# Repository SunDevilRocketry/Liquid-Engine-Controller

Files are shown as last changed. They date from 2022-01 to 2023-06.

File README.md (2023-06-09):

<h1>Liquids Engine Controller</h1>

<p>Current PCB Revision: 5.1</p>
<p>PCB Part Number: L0002</p>

<p>The Liquid Engine Controller is the main embedded processor of Sun Devil Rocketry's Liquid Engine. As the brains of the engine, the controller is responsible for executing propellant feed sequences semi-autonomously, logging sensor data, and transmitting engine telemetry. The controller is equipped with an STM32 ARM Cortex M7 processor and 4Mb of external flash for data logging. The board includes a micro-SD card jack for easy access to the logged data. The board includes many power sources for flexible use of the controller during testing and normal operation. These include a 12V power jack, a USB Type B connector, and a 2-pin male pin header. The board includes short circuit protection on the main power rail and regulates the multiplexed supply to 5V and 3.3V with a buck converter and linear regulator (LDO) respectively. The board interfaces with a PC through either the USB port or the 8-pin telemetry connector, which allows wireless transceiver modules with either a UART or SPI interface to be connected. The screw terminals on the board connect to the ignition circuitry. An e-match is used to initiate combustion, and two continuity wires are used to provide the controller feedback on the ignition state. The ignition current is routed through an additional screw terminal which serves as a safety/arming switch. The board interfaces with all of the engine sensors, including eight pressure transducers, a thermocouple, and a load cell. The pressure transducer outputs are amplified with a programmable-gain instrumentation amplifier, which allows for up to 256 calibration settings. The thermocouple output is processed using a cold-junction compensation IC. Additionally, the board includes a reset button and several LEDs for visual indication of power and firmware status.
</p>

<p><b>Working Directory Structure:</b></p>

<p>
   cad: 3d models

   doc: documentation

   img: images of circuit/footprints for github display 
   
   lib: libraries for schematic symbols and footprints

   production: files needed for pcb fabrication, e.g. gerbers, profile, drill file

   sim: simulation models/files 

   src: source design files, e.g. schematic and PCB layout files
</p>

<h2>3D Model: </h2>

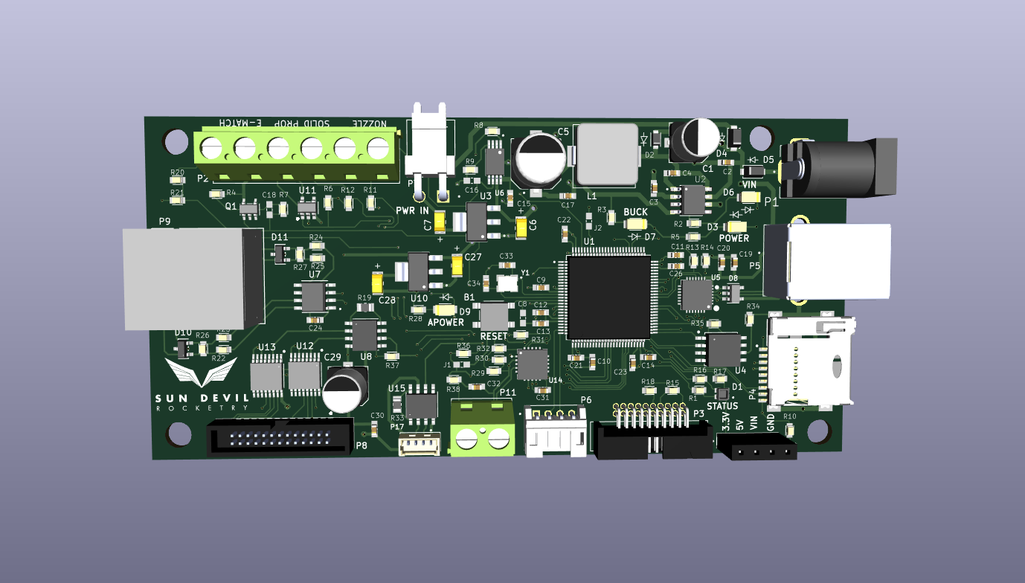
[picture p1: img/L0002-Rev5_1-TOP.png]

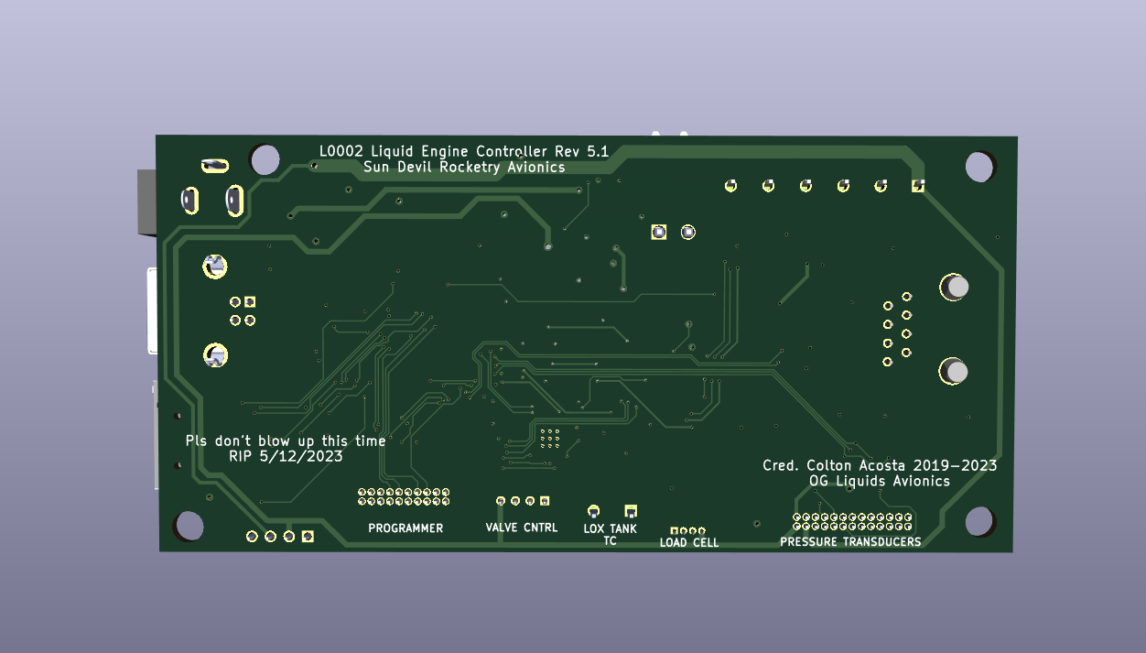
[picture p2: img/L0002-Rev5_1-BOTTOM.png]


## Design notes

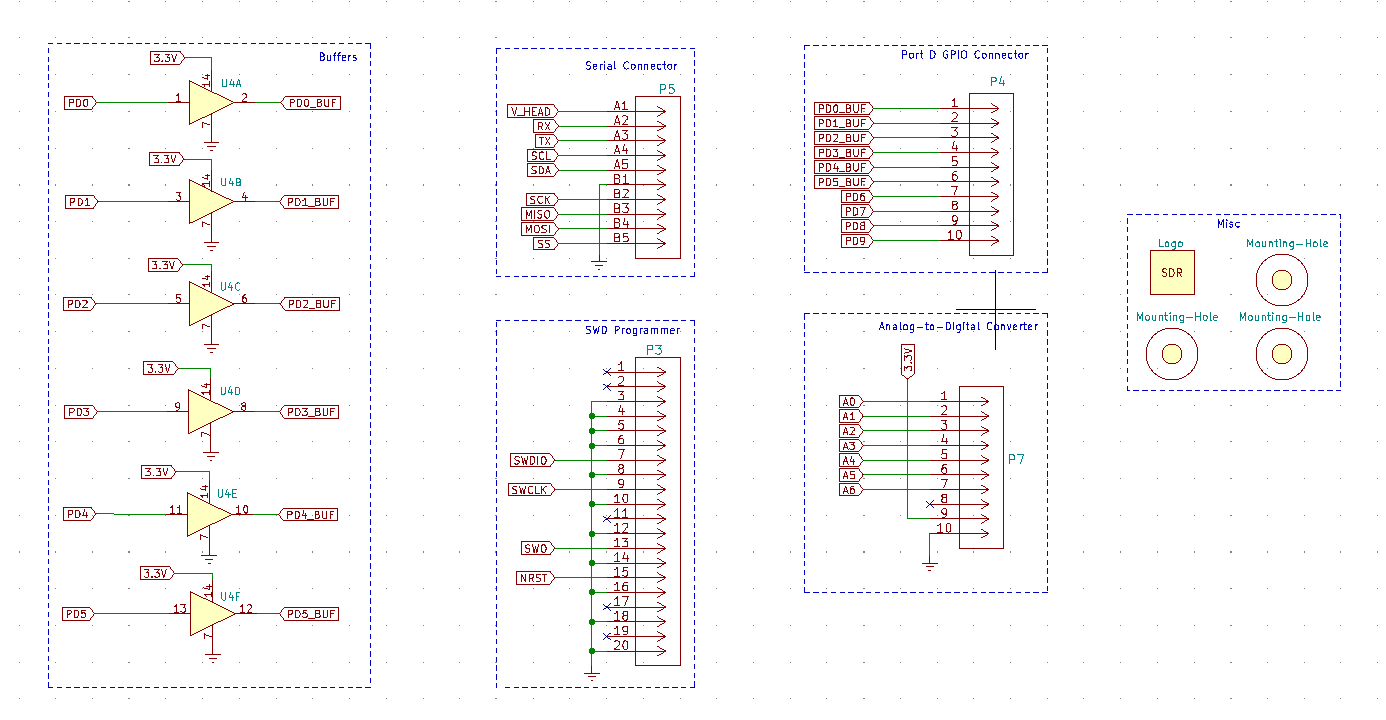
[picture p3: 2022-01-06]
img/Connectors-Schematic.png

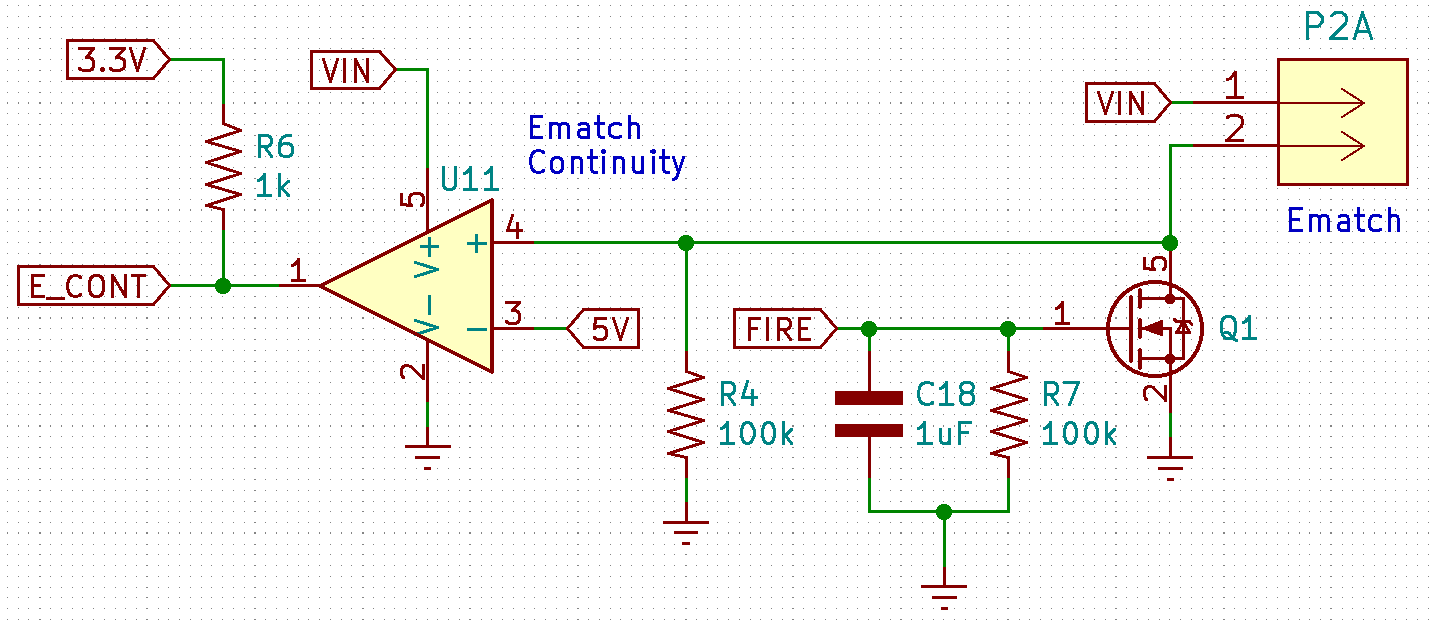
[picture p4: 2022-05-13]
img/Ignition-Schematic.png

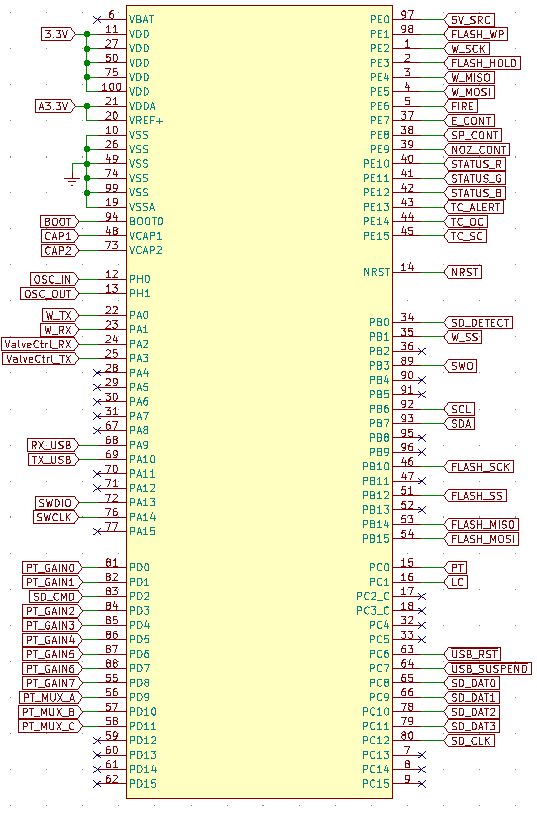
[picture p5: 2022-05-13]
img/MCU-Schematic.png

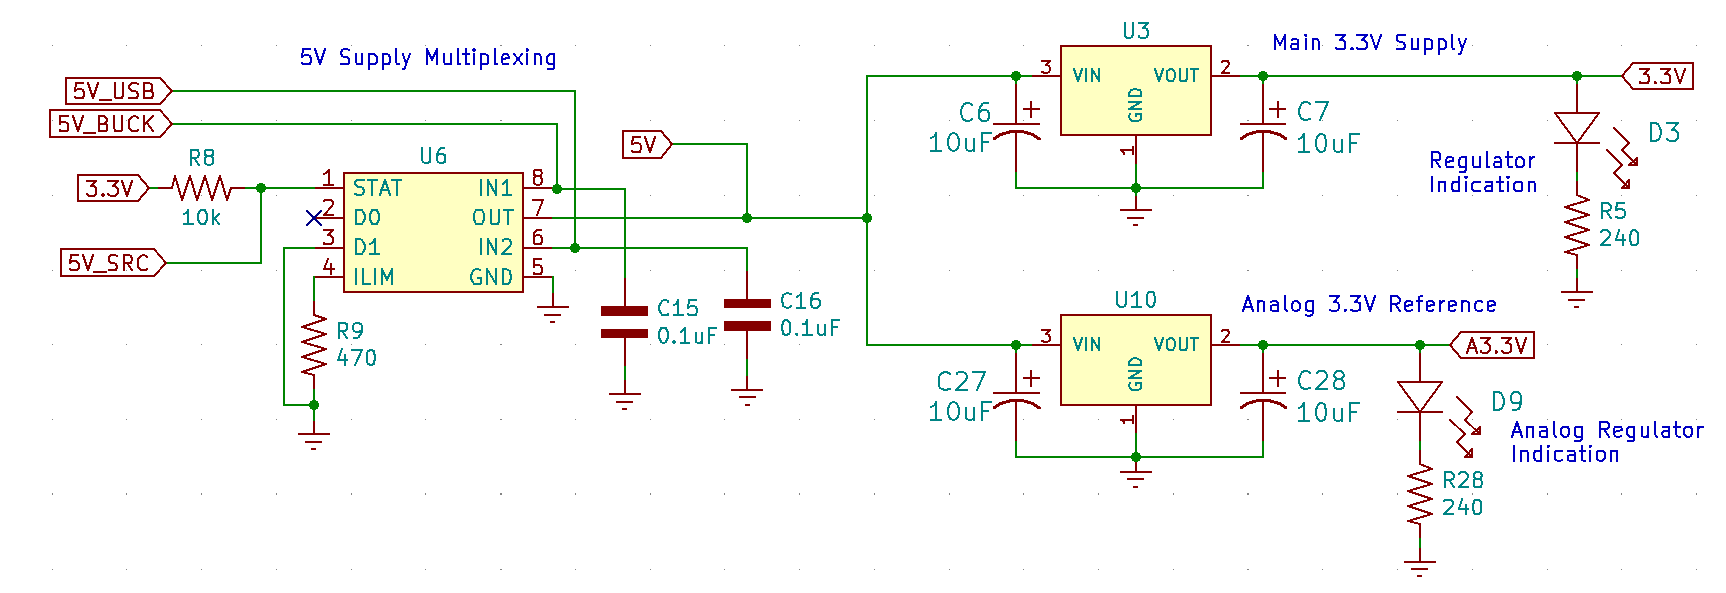
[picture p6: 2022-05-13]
img/3V3-Schematic.png

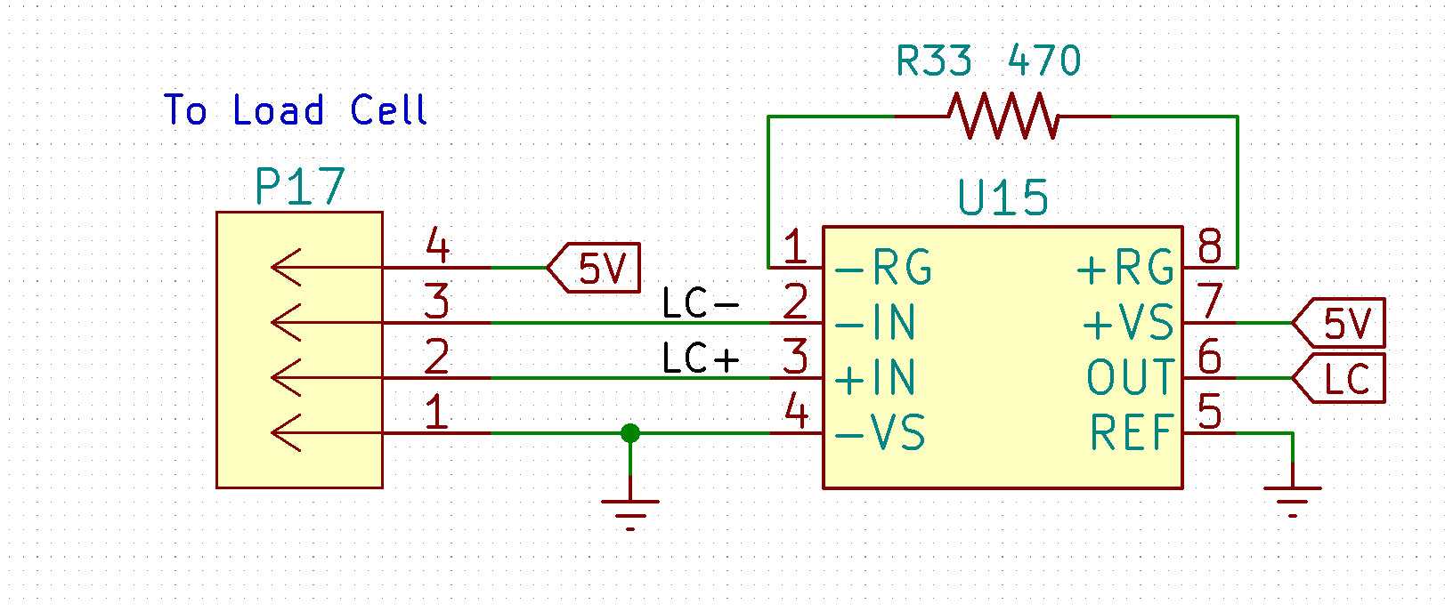
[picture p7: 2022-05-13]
img/Load-Cell-Schematic.png

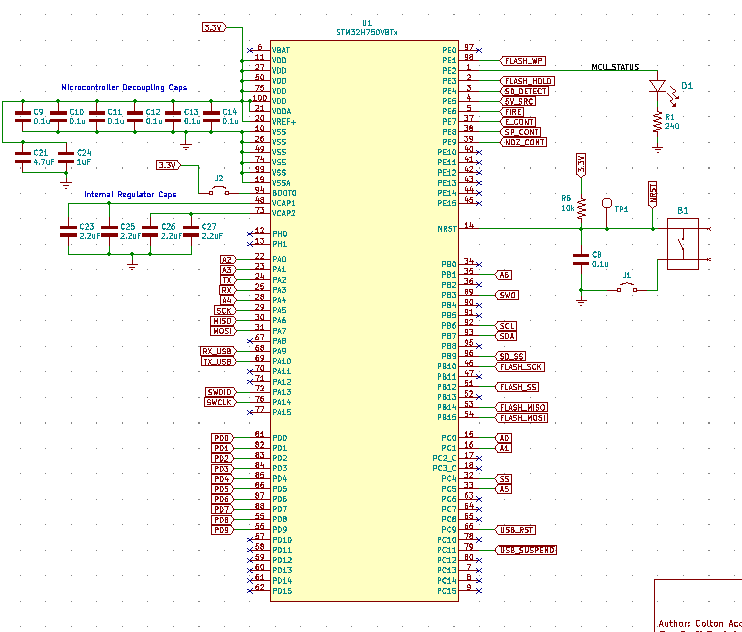
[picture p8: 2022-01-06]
img/Micro-Schematic.png

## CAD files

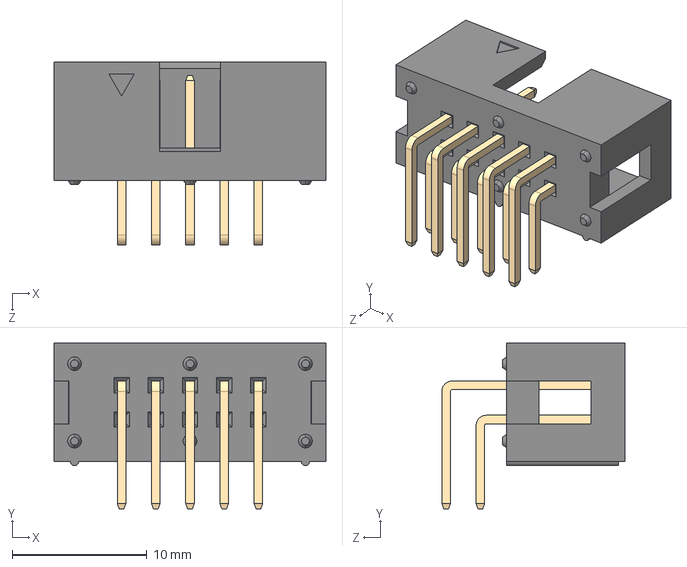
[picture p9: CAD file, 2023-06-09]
CAD/3Dfiles/SBH11-PBPC-D05-RA-BK.STEP
20.2 x 12.3 x 13.6 mm

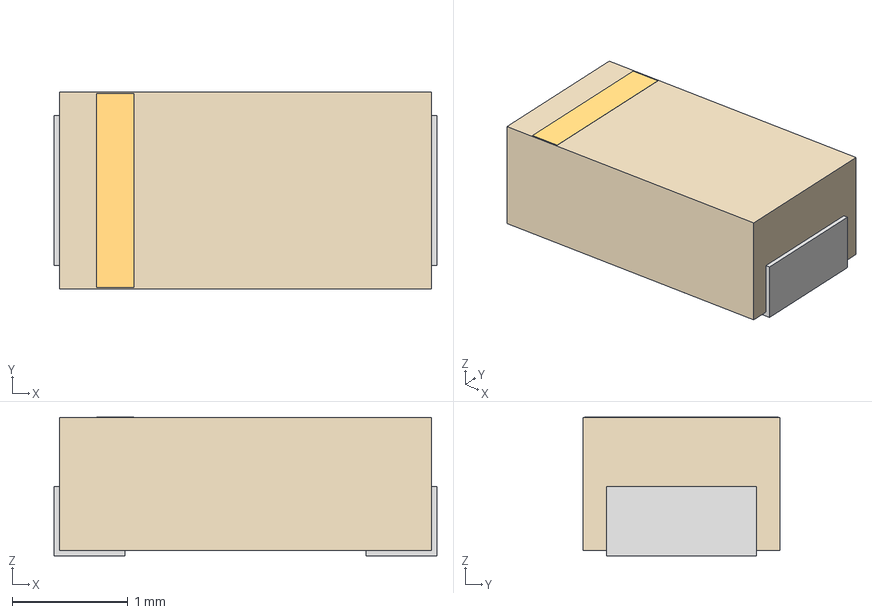
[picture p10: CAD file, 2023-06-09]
CAD/3Dfiles/LED_LTST-C150GKT_LTO.step
3.30 x 1.70 x 1.20 mm

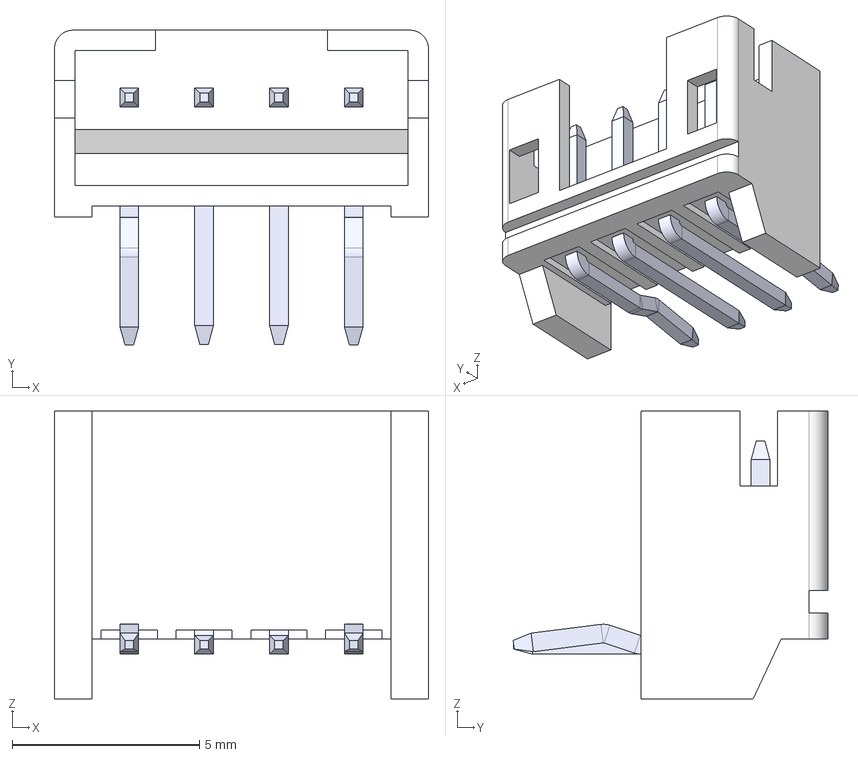
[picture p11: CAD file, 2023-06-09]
CAD/3Dfiles/140-504-415-000.step
10.0 x 8.41 x 7.70 mm
RA Housing_504
RA Contact_Kink
RA Contact_Str
RA Contact_Str001
RA Contact_Kink001

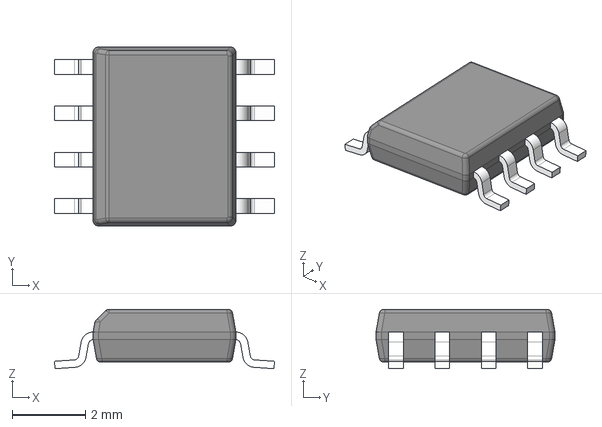
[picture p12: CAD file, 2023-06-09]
CAD/3Dfiles/sn65hcd71.step
6.02 x 4.90 x 1.63 mm
BODY-SO
LEAD-D0008A x 8

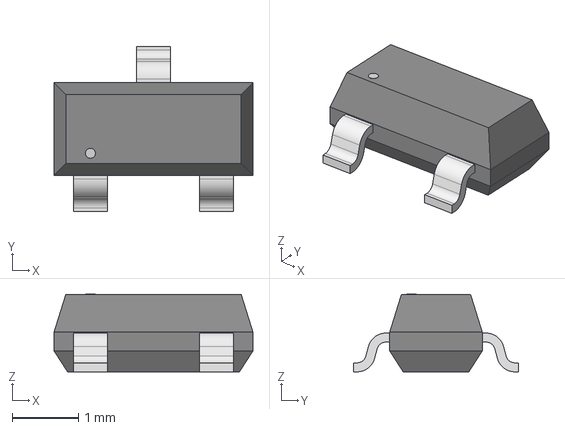
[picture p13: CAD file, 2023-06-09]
CAD/3Dfiles/CDSOT23-SM712.step
3.00 x 2.49 x 1.17 mm

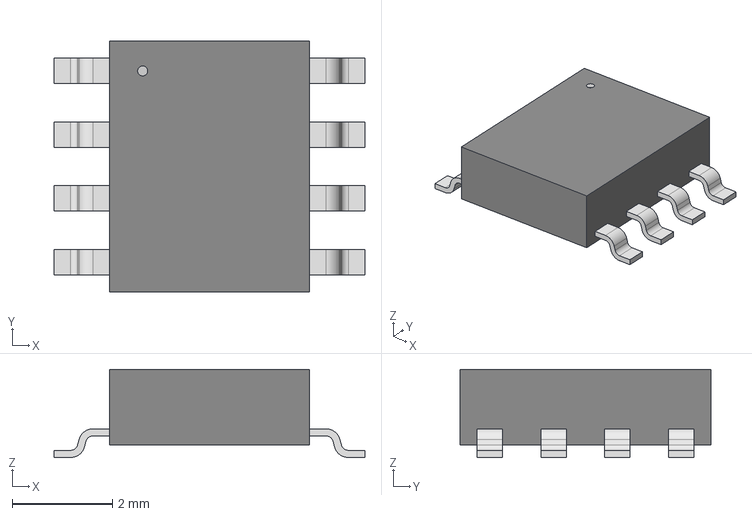
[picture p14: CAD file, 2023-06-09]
CAD/3Dfiles/AD623ARZ-R7.step
6.20 x 5.00 x 1.75 mm

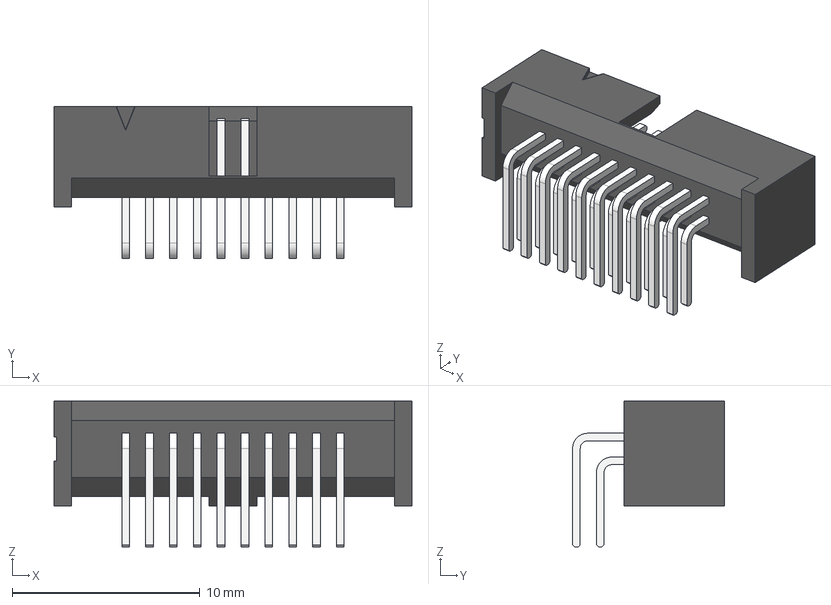
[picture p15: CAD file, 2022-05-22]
CAD/3Dfiles/3220-20-0200-00.stp
19.1 x 8.08 x 7.75 mm
_SHF-110-01-D_header
_SHF-First_Position_Indicator
_T-1S71-02-10-D-RA

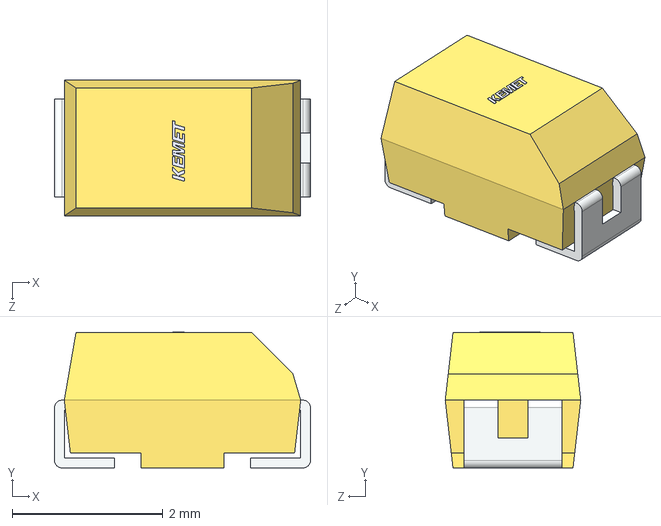
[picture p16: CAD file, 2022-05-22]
CAD/3Dfiles/T491A106K010AT.step
3.40 x 1.81 x 1.80 mm

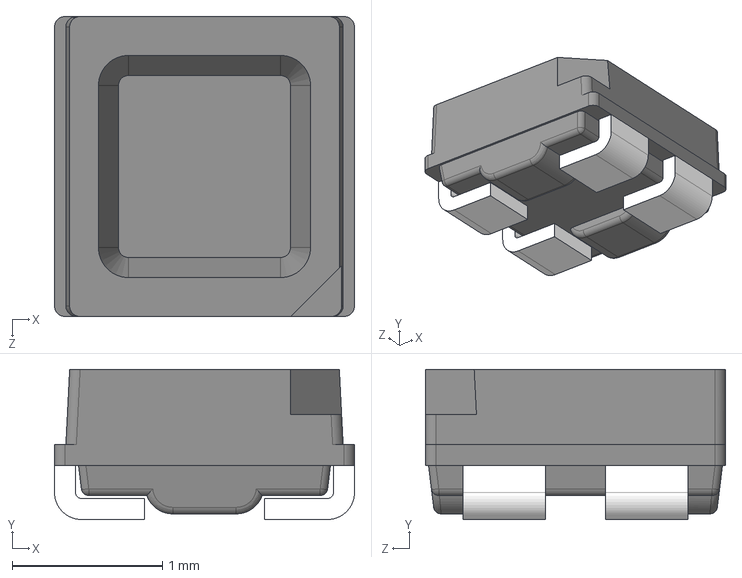
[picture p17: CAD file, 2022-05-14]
CAD/3Dfiles/CLMVC-FKA-CL1D1L71BB7C3C3.STEP
2.00 x 1 x 2.00 mm

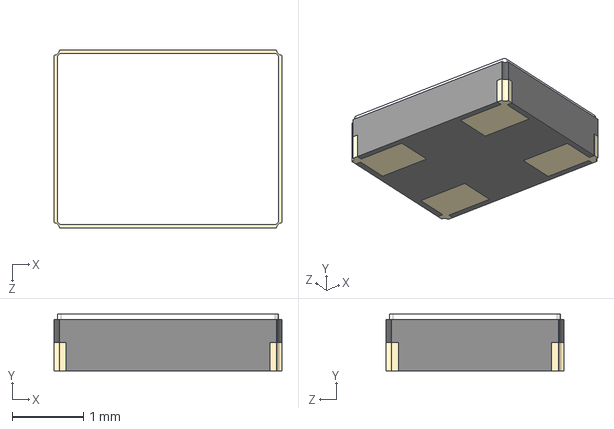
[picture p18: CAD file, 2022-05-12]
CAD/3Dfiles/ECS-240-18-33-JGN-TR.STEP
3.20 x 0.8 x 2.50 mm

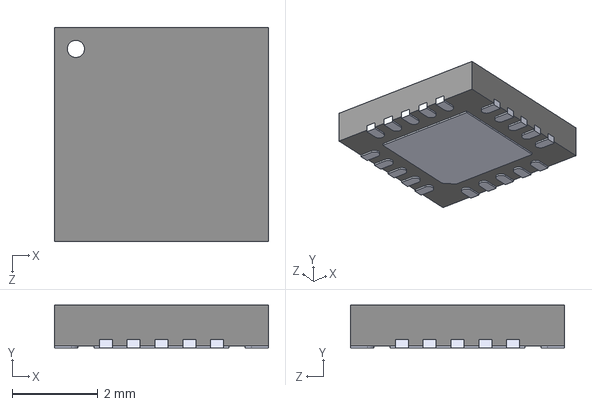
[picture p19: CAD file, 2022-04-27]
CAD/3Dfiles/MCP96L01T-E_MX.step
5.00 x 1.00 x 5.00 mm

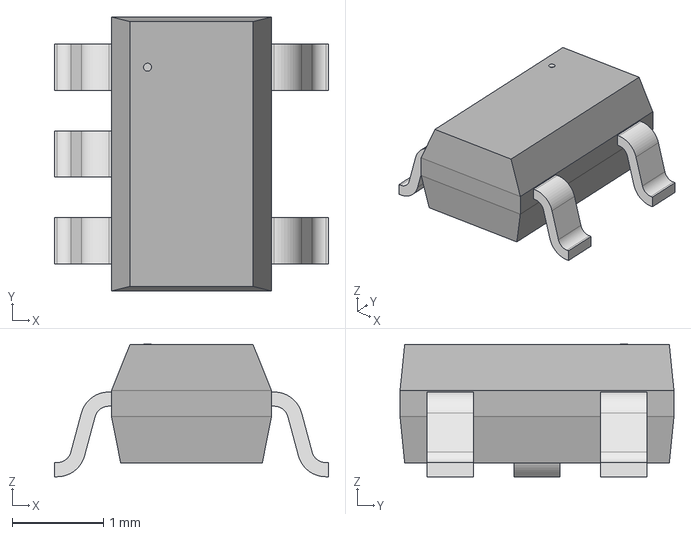
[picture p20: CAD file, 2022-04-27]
CAD/3Dfiles/TS391lYLT.step
3.00 x 3.00 x 1.45 mm

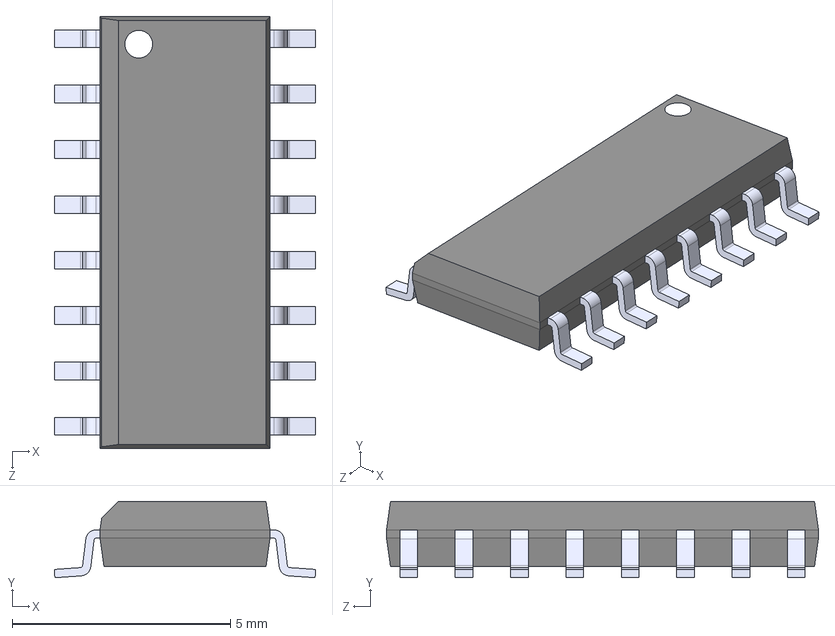
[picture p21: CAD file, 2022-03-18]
CAD/3Dfiles/CD74HC238M.STEP
5.99 x 1.75 x 9.91 mm

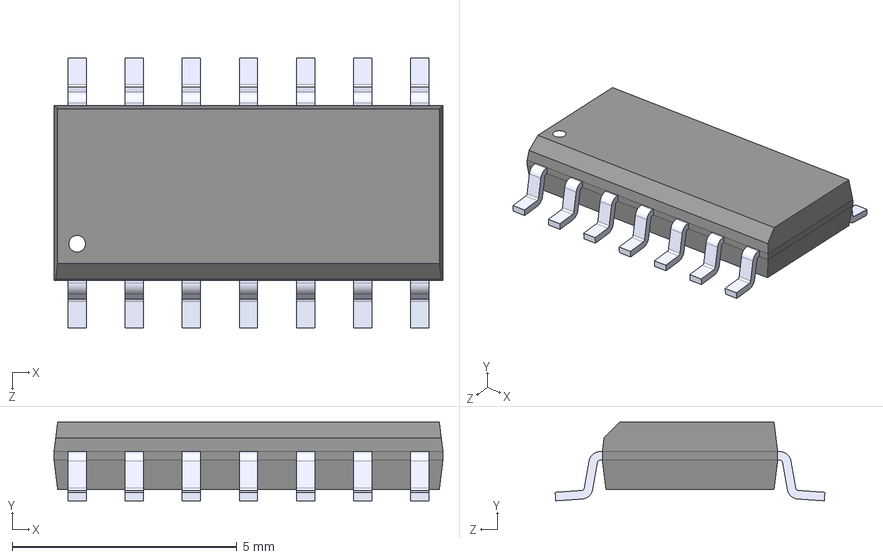
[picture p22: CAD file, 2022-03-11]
CAD/3Dfiles/MC74HC4066ADG.step
8.65 x 1.75 x 6.00 mm

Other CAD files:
CAD/3Dfiles/MAX4617EUE.step
CAD/3Dfiles/SRP1038A-330M.stp
CAD/3Dfiles/SP0504BAHTG.step
CAD/3Dfiles/SBH11-PBPC-D10-RA-BK.stp
CAD/3Dfiles/039299043.step
CAD/3Dfiles/039299043.stl
CAD/3Dfiles/1727078.step
CAD/3Dfiles/1761682-3.stp
CAD/3Dfiles/20021511-00026XXLFC.step
CAD/3Dfiles/282837-2.step
CAD/3Dfiles/282837-6.STEP
CAD/3Dfiles/5015680807.stp
CAD/3Dfiles/530470410.step
CAD/3Dfiles/532580229.stp
CAD/3Dfiles/54602-908LFc.stp
CAD/3Dfiles/647676-2.step
CAD/3Dfiles/66953-005LF_AMP.step
CAD/3Dfiles/901471110.stp
CAD/3Dfiles/CAP_0603.step
CAD/3Dfiles/CAP_UKL_5X11_NCH.step
CAD/3Dfiles/CBC3225T220KR.STEP
CAD/3Dfiles/CP2102-GMR_QFN28.step
CAD/3Dfiles/CWR11_C__KEM.step
CAD/3Dfiles/DIO_RB160VAM_ROM.step
CAD/3Dfiles/EEEFP1E151AL.STEP
CAD/3Dfiles/EEEFPV680XAP.step
CAD/3Dfiles/EJ508A.step
CAD/3Dfiles/ERJ-6GEYJ474V.STEP
CAD/3Dfiles/FT312D-32L1C-R.stp
CAD/3Dfiles/LMS8117AMP-3.3NOPB.STEP
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

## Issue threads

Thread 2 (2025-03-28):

Engine Controller LORA Module

dmortloff, 2025-03-28:
LORA would potentially be a nice addition to have to the engine controller for remote access and utilization.

For this project, tasks would be designing a schematic for the LORA module (Realistically the one previously used in the Flight Computer) and adding the schematic to the overall PCB

superN8, 2025-09-26:
Im trying to find an alternate LoRa module, hopefully something newer with better documentation.
I want it to have an MMCX connector so we can remove the antenna connector from the PCB and also avoid interference with other signals in the PCB.
Here is an example of the kind of thing I'm looking into
[https://www.digikey.com/en/products/detail/seeed-technology-co-ltd/114993390/27563010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](url)

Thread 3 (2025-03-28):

Design SDR RF Module

dmortloff, 2025-03-28:
SDR has been using preassembled RF chips for quite some time now.

Designing our own RF modules would be cheaper, as well as a cool project

1. Research the board: We need to know what we need and how to optimize it, and how to make it fit onto our existing boards
2. Design the board: We need a small and efficient board to be able to function optimally
3. Replace:Hopefully, it will work so well we can use it on the Flight Computer and other applications

This is a very theoretical project, and will be on backburner for a while and worked on when possible.

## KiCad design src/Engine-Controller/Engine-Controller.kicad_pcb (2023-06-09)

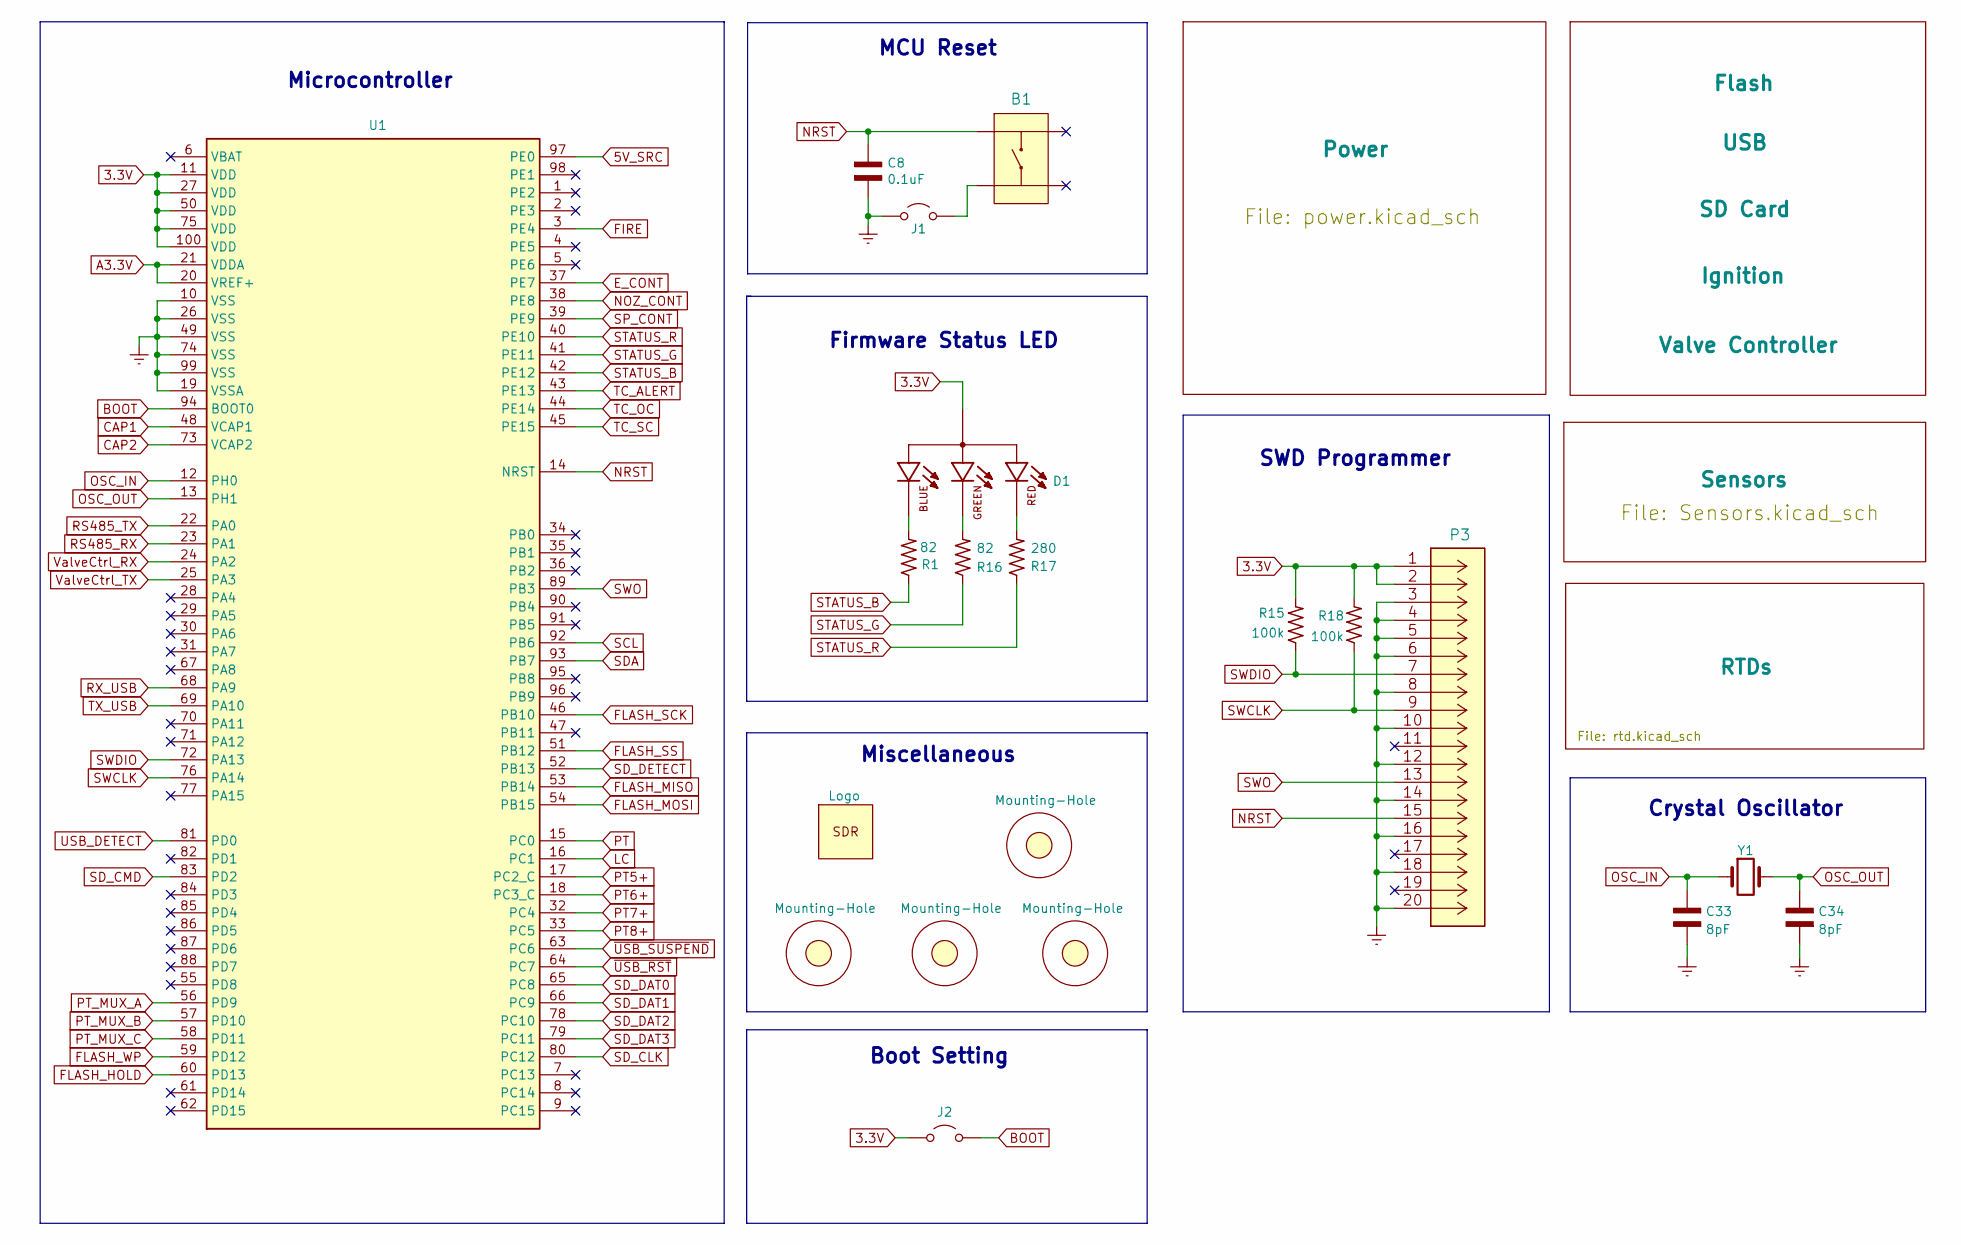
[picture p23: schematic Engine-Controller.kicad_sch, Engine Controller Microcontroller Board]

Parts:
B1: PTS647SM38SMTR2LFS
C8: 0.1uF; CAP_0603
C33, C34: 8pF; CAP_0603
D1: CLMVC-FKA-CL1D1L71BB7C3C3
H1, H4, H5, H6: Mounting-Hole; MountingHole_4.3mm_M4_DIN965
J1, J2: Jumper_NO; Jumper-NO
LOGO2: Logo
P3: 3220-20-0200-00
R1, R16: 82; RES_0603
R15, R18: 100k; RES_0603
R17: 280; RES_0603
U1: STM32H750VBTx; STM32H750VBT6
Y1: ECS-240-18-33-JGN-TR

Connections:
3.3V: D1.1, J2.1 (A), P3.1, P3.2, R15.2, R18.2, U1.11 (VDD), U1.27 (VDD), U1.50 (VDD), U1.75 (VDD), U1.100 (VDD); also elsewhere on the board
5V_SRC: U1.97 (PE0); also elsewhere on the board
A3.3V: U1.20 (VREF+), U1.21 (VDDA); also elsewhere on the board
BOOT: J2.2 (B), U1.94 (BOOT0)
CAP1: U1.48 (VCAP1); also elsewhere on the board
CAP2: U1.73 (VCAP2); also elsewhere on the board
E_CONT: U1.37 (PE7); also elsewhere on the board
Earth: C8.1, C33.2, C34.2, J1.1 (A), P3.3, P3.4, P3.5, P3.6, P3.8, P3.10, P3.12, P3.14, P3.16, P3.18, P3.20, U1.10 (VSS), U1.19 (VSSA), U1.26 (VSS), U1.49 (VSS), U1.74 (VSS), U1.99 (VSS); also elsewhere on the board
FIRE: U1.3 (PE4); also elsewhere on the board
FLASH_HOLD: U1.60 (PD13); also elsewhere on the board
FLASH_MISO: U1.53 (PB14); also elsewhere on the board
FLASH_MOSI: U1.54 (PB15); also elsewhere on the board
FLASH_SCK: U1.46 (PB10); also elsewhere on the board
FLASH_SS: U1.51 (PB12); also elsewhere on the board
FLASH_WP: U1.59 (PD12); also elsewhere on the board
LC: U1.16 (PC1); also elsewhere on the board
NOZ_CONT: U1.38 (PE8); also elsewhere on the board
NRST: B1.3, C8.2, P3.15, U1.14 (NRST)
unnamed: D1.2, R1.2
unnamed: D1.3, R16.2
unnamed: D1.4, R17.2
unnamed: B1.1, J1.2 (B)
OSC_IN: C33.1, U1.12 (PH0), Y1.1
OSC_OUT: C34.1, U1.13 (PH1), Y1.3
PT: U1.15 (PC0); also elsewhere on the board
PT5+: U1.17 (PC2_C); also elsewhere on the board
PT6+: U1.18 (PC3_C); also elsewhere on the board
PT7+: U1.32 (PC4); also elsewhere on the board
PT8+: U1.33 (PC5); also elsewhere on the board
PT_MUX_A: U1.56 (PD9); also elsewhere on the board
PT_MUX_B: U1.57 (PD10); also elsewhere on the board
PT_MUX_C: U1.58 (PD11); also elsewhere on the board
RS485_RX: U1.23 (PA1); also elsewhere on the board
RS485_TX: U1.22 (PA0); also elsewhere on the board
RX_USB: U1.68 (PA9); also elsewhere on the board
SCL: U1.92 (PB6); also elsewhere on the board
SDA: U1.93 (PB7); also elsewhere on the board
SD_CLK: U1.80 (PC12); also elsewhere on the board
SD_CMD: U1.83 (PD2); also elsewhere on the board
SD_DAT0: U1.65 (PC8); also elsewhere on the board
SD_DAT1: U1.66 (PC9); also elsewhere on the board
SD_DAT2: U1.78 (PC10); also elsewhere on the board
SD_DAT3: U1.79 (PC11); also elsewhere on the board
SD_DETECT: U1.52 (PB13); also elsewhere on the board
SP_CONT: U1.39 (PE9); also elsewhere on the board
STATUS_B: R1.1, U1.42 (PE12)
STATUS_G: R16.1, U1.41 (PE11)
STATUS_R: R17.1, U1.40 (PE10)
SWCLK: P3.9, R18.1, U1.76 (PA14)
SWDIO: P3.7, R15.1, U1.72 (PA13)
SWO: P3.13, U1.89 (PB3)
TC_ALERT: U1.43 (PE13); also elsewhere on the board
TC_OC: U1.44 (PE14); also elsewhere on the board
TC_SC: U1.45 (PE15); also elsewhere on the board
TX_USB: U1.69 (PA10); also elsewhere on the board
USB_DETECT: U1.81 (PD0); also elsewhere on the board
ValveCtrl_RX: U1.24 (PA2); also elsewhere on the board
ValveCtrl_TX: U1.25 (PA3); also elsewhere on the board
~USB_RST: U1.64 (PC7); also elsewhere on the board
~USB_SUSPEND: U1.63 (PC6); also elsewhere on the board

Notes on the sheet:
SWD Programmer
Miscellaneous
Crystal Oscillator
Microcontroller
Boot Setting
Firmware Status LED
MCU Reset

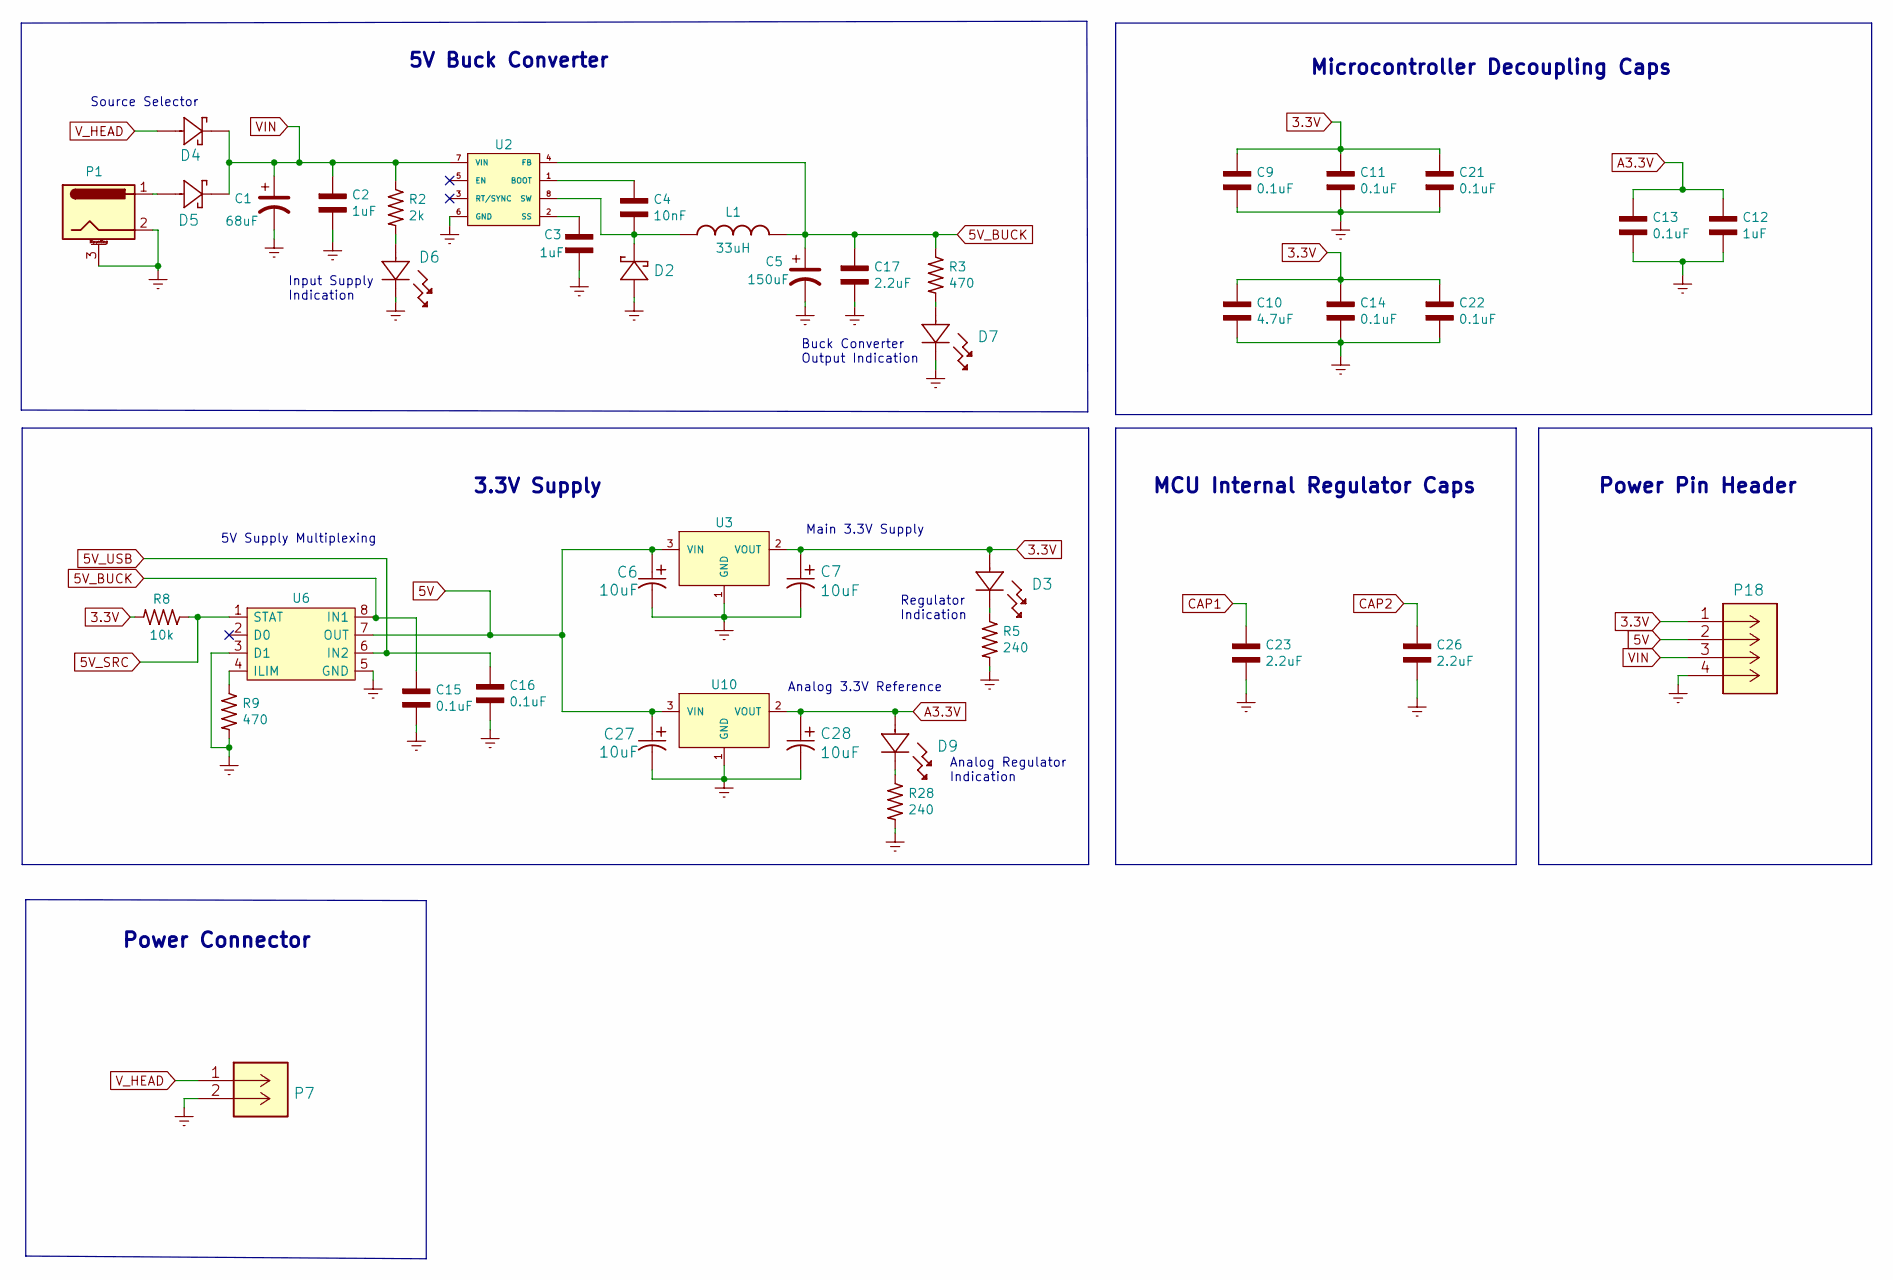
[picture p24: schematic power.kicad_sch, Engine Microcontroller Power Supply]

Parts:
C1: 68uF; EEEFPV680XAP
C2, C3, C12: 1uF; CAP_0603
C4: 10nF; CAP_0603
C5: 150uF; EEEFP1E151AL
C6, C7, C27, C28: 10uF; T491A106K010AT
C9, C11, C13, C14, C15, C16, C21, C22: 0.1uF; CAP_0603
C10: 4.7uF; CAP_0603
C17, C23, C26: 2.2uF; CAP_0603
D2: RB160VAM-60TR
D3, D6, D7, D9: SML-LX1206GC-TR
D4, D5: SM5819PL-TP
L1: 33uH; SRP1038A-330M
P1: EJ508A; 12V_power_jack
P7: 647676-2
P18: PPTC041LFBN-RC
R2: 2k; RES_0603
R3, R9: 470; RES_0603
R5, R28: 240; RES_0603
R8: 10k; RES_0603
U2: LM22672MRE-5.0_NOPB
U3, U10: LMS8117AMP-3.3_NOPB; LMS8117AMP-3.3NOPB
U6: TPS2115APWR

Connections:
3.3V: C7.1, C9.2, C10.2, C11.2, C14.2, C21.2, C22.2, D3.2, P18.1 (+12V), R8.2, U3.2 (VOUT); also elsewhere on the board
5V: C6.1, C27.1, P18.2 (GND), U3.3 (VIN), U6.7 (OUT), U10.3 (VIN); also elsewhere on the board
5V_BUCK: C5.1, C15.2, C17.2, L1.2, R3.1, U2.4 (FB), U6.8 (IN1)
5V_SRC: R8.1, U6.1 (STAT); also elsewhere on the board
5V_USB: C16.2, U6.6 (IN2); also elsewhere on the board
A3.3V: C12.2, C13.2, C28.1, D9.2, U10.2 (VOUT); also elsewhere on the board
CAP1: C23.2; also elsewhere on the board
CAP2: C26.2; also elsewhere on the board
Earth: C1.2, C2.1, C3.1, C5.2, C6.2, C7.2, C9.1, C10.1, C11.1, C12.1, C13.1, C14.1, C15.1, C16.1, C17.1, C21.1, C22.1, C23.1, C26.1, C27.2, C28.2, D2.2, D6.1, D7.1, P1.2, P1.3 (MountPin), P7.2, P18.4, R5.2, R9.2, R28.2, U2.6 (GND), U3.1 (GND), U6.3 (D1), U6.5 (GND), U10.1 (GND); also elsewhere on the board
unnamed: D3.1, R5.1
unnamed: D5.2, P1.1
unnamed: D6.2, R2.2
unnamed: D7.2, R3.2
unnamed: D9.1, R28.1
unnamed: C4.2, U2.1 (BOOT)
unnamed: C3.2, U2.2 (SS)
unnamed: C4.1, D2.1, L1.1, U2.8 (SW)
unnamed: R9.1, U6.4 (ILIM)
VIN: C1.1, C2.2, D4.1, D5.1, P18.3, R2.1, U2.7 (VIN); also elsewhere on the board
V_HEAD: D4.2, P7.1

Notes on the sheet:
Power Connector
Power Pin Header
5V Buck Converter
5V Supply Multiplexing
Main 3.3V Supply
Analog Regulator Indication
Regulator Indication
Buck Converter Output Indication
Microcontroller Decoupling Caps
Input Supply Indication
Analog 3.3V Reference
3.3V Supply
Source Selector
MCU Internal Regulator Caps

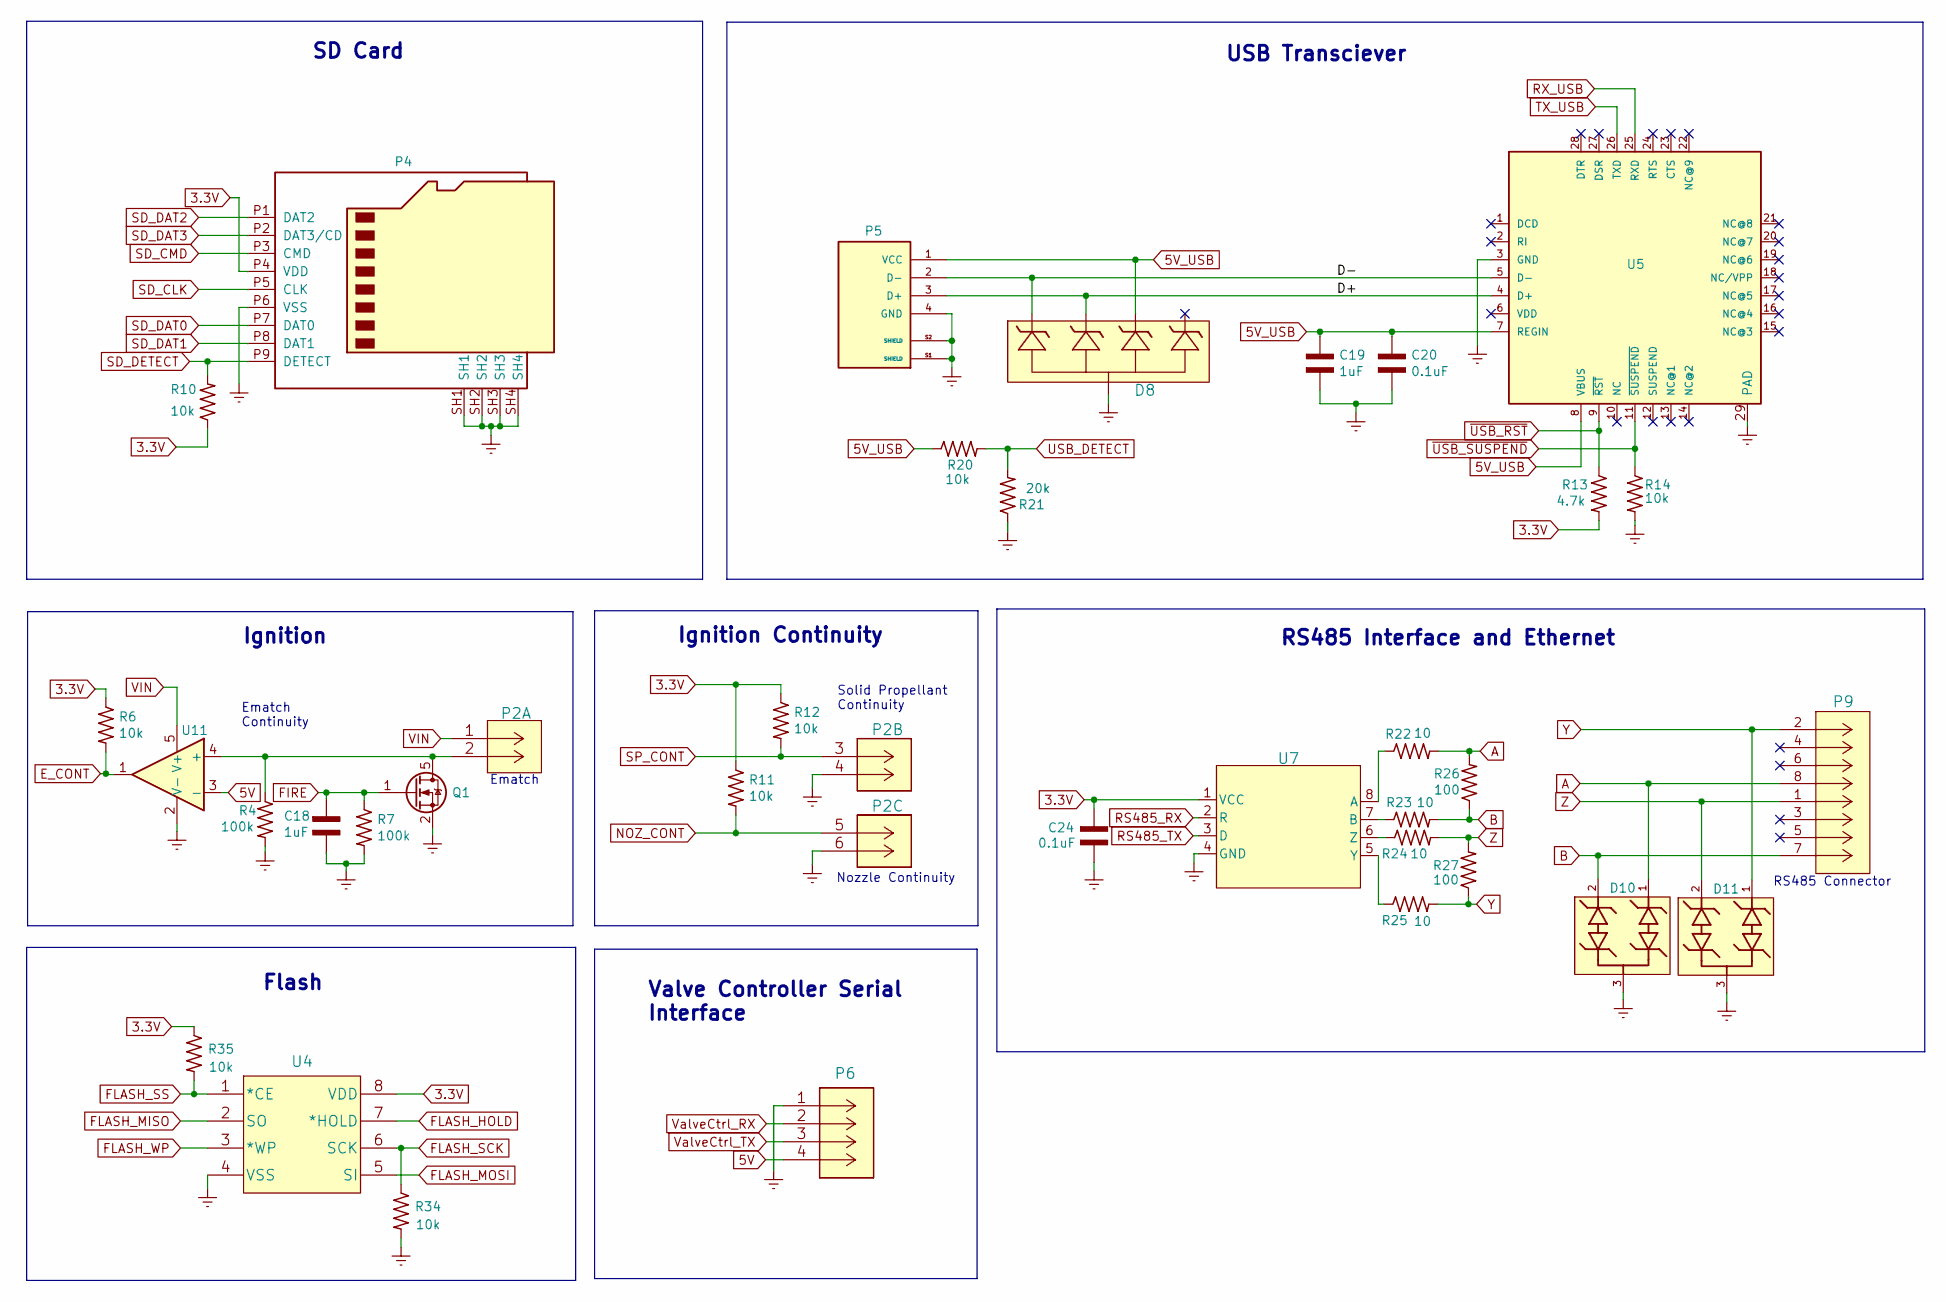
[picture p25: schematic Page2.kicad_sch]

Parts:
C18, C19: 1uF; CAP_0603
C20, C24: 0.1uF; CAP_0603
D8: SP0504BAHTG
D10, D11: SMBJ36CA-13-F; CDSOT23-SM712; PARTREV 20-2
P2: 282837-6
P4: Micro_SD_Card; MEM2075-00-140-01-A
P5: USB; USB-TypeB
P6: 140-504-415-000
P9: 54602-908LF
Q1: QS5U17TR
R4, R7: 100k; RES_0603
R6, R10, R11, R12, R14, R20, R34, R35: 10k; RES_0603
R13: 4.7k; RES_0603
R21: 20k; RES_0603
R22, R23, R24, R25: 10; RES_0603
R26, R27: 100; RES_0603
U4: SST25VF040B-50-4I-S2AE-T
U5: CP2102-GMR(QFN28); CP2012-GMR; MPN CP2102-GMR
U7: SN65HVD71DR
U11: TS391IYLT

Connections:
3.3V: C24.2, P4.P4 (VDD), R6.1, R10.1, R11.1, R12.1, R13.2, R35.1, U4.8 (VDD), U7.1 (VCC); also elsewhere on the board
5V: P6.4, U11.3 (-); also elsewhere on the board
5V_USB: C19.2, C20.2, D8.4, P5.1 (VCC), R20.1, U5.7 (REGIN), U5.8 (VBUS); also elsewhere on the board
/Page2/D+: D8.3, P5.3 (D+), U5.4 (D+)
/Page2/D-: D8.1, P5.2 (D-), U5.5 (D-)
A: D10.1, P9.8, R22.2, R26.2
B: D10.2, P9.7, R23.2, R26.1
E_CONT: R6.2, U11.1; also elsewhere on the board
Earth: C18.1, C19.1, C20.1, C24.1, D8.2, D10.3, D11.3, P2.4 (6), P2.6, P4.P6 (VSS), P4.SH1, P4.SH2, P4.SH3, P4.SH4, P5.4 (GND), P5.S1 (SHIELD), P5.S2 (SHIELD), P6.1 (+12V), Q1.2 (S), R4.2, R7.2, R14.2, R21.1, R34.2, U4.4 (VSS), U5.3 (GND), U5.29 (PAD), U7.4 (GND), U11.2 (V-); also elsewhere on the board
FIRE: C18.2, Q1.1 (G), R7.1; also elsewhere on the board
FLASH_HOLD: U4.7 (*HOLD); also elsewhere on the board
FLASH_MISO: U4.2 (SO); also elsewhere on the board
FLASH_MOSI: U4.5 (SI); also elsewhere on the board
FLASH_SCK: R34.1, U4.6 (SCK); also elsewhere on the board
FLASH_SS: R35.2, U4.1 (*CE); also elsewhere on the board
FLASH_WP: U4.3 (*WP); also elsewhere on the board
NOZ_CONT: P2.5, R11.2; also elsewhere on the board
unnamed: P2.2 (6), Q1.5 (D), R4.1, U11.4 (+)
unnamed: R22.1, U7.8 (A)
unnamed: R23.1, U7.7 (B)
unnamed: R25.1, U7.5 (Y)
unnamed: R24.1, U7.6 (Z)
RS485_RX: U7.2 (R); also elsewhere on the board
RS485_TX: U7.3 (D); also elsewhere on the board
RX_USB: U5.25 (RXD); also elsewhere on the board
SD_CLK: P4.P5 (CLK); also elsewhere on the board
SD_CMD: P4.P3 (CMD); also elsewhere on the board
SD_DAT0: P4.P7 (DAT0); also elsewhere on the board
SD_DAT1: P4.P8 (DAT1); also elsewhere on the board
SD_DAT2: P4.P1 (DAT2); also elsewhere on the board
SD_DAT3: P4.P2 (DAT3/CD); also elsewhere on the board
SD_DETECT: P4.P9 (DETECT), R10.2; also elsewhere on the board
SP_CONT: P2.3 (5), R12.2; also elsewhere on the board
TX_USB: U5.26 (TXD); also elsewhere on the board
USB_DETECT: R20.2, R21.2; also elsewhere on the board
VIN: P2.1 (5), U11.5 (V+); also elsewhere on the board
ValveCtrl_RX: P6.2 (GND); also elsewhere on the board
ValveCtrl_TX: P6.3; also elsewhere on the board
Y: D11.1, P9.2, R25.2, R27.1
Z: D11.2, P9.1, R24.2, R27.2
~USB_RST: R13.1, U5.9 (~RST); also elsewhere on the board
~USB_SUSPEND: R14.1, U5.11 (~SUSPEND); also elsewhere on the board

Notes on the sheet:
SD Card
RS485 Connector
Ematch
RS485 Interface and Ethernet
USB Transciever
Ignition Continuity
Ematch Continuity
Ignition
Flash
Nozzle Continuity
Solid Propellant Continuity
Valve Controller Serial Interface

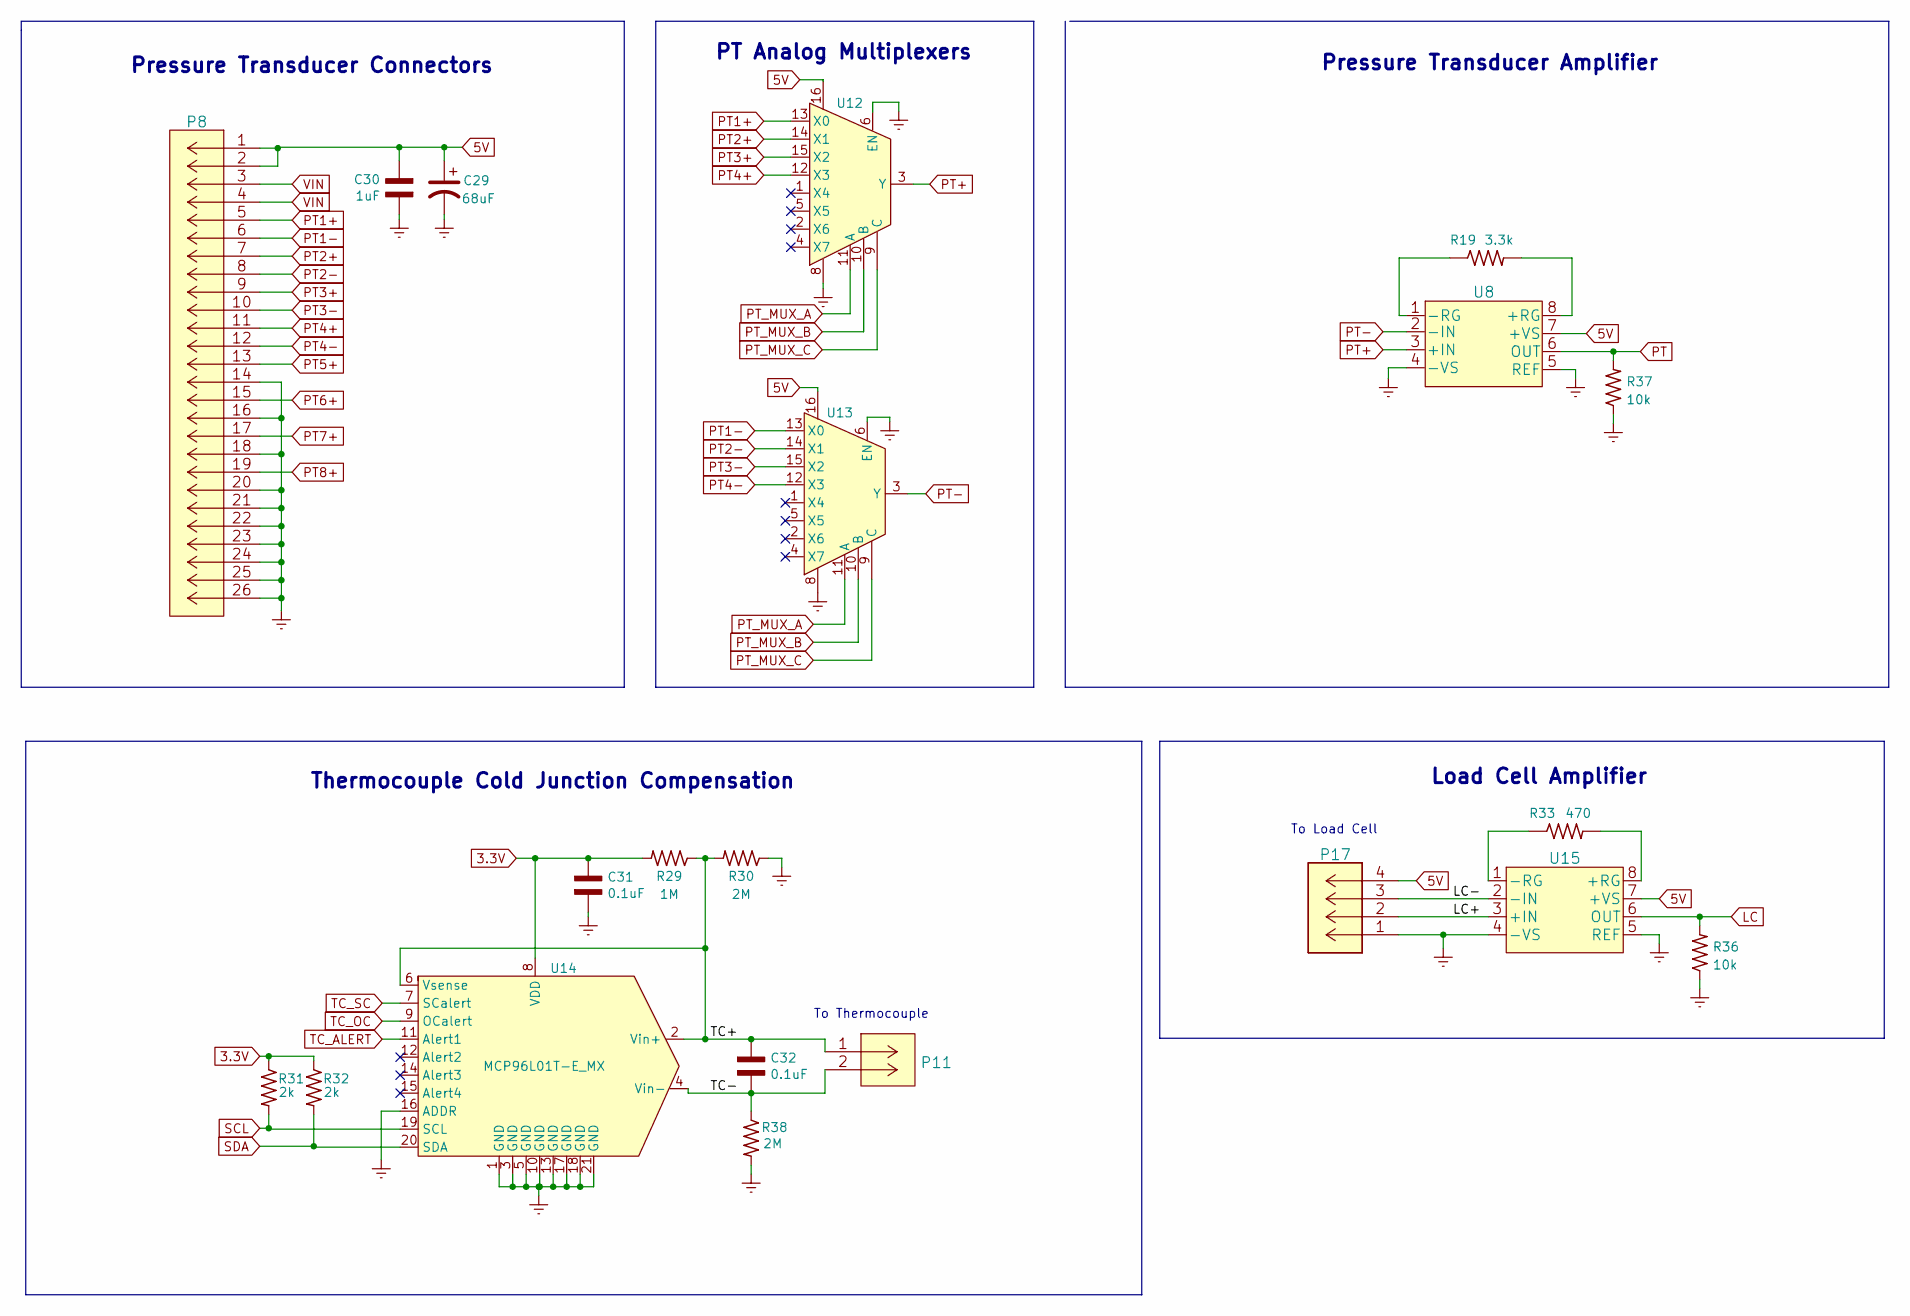
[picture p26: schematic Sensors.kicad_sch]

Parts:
C29: 68uF; EEEFPV680XAP
C30: 1uF; CAP_0603
C31, C32: 0.1uF; CAP_0603
P8: 20021511-00026T4LF
P11: 282837-2
P17: 0530470410
R19: 3.3k; RES_0805
R29: 1M; RES_0603
R30, R38: 2M; RES_0603
R31, R32: 2k; RES_0603
R33: 470; RES_0805
R36, R37: 10k; RES_0603
U8, U15: AD623ARZ-R7
U12, U13: MAX4617EUE+T; max4617eue
U14: MCP96L01T-E_MX

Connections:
3.3V: C31.2, R29.2, R31.1, R32.1, U14.8 (VDD); also elsewhere on the board
5V: C29.1, C30.2, P8.1, P8.2, P17.4, U8.7 (+VS), U12.16, U13.16, U15.7 (+VS); also elsewhere on the board
/Sensors/LC+: P17.2 (GND), U15.3 (+IN)
/Sensors/LC-: P17.3, U15.2 (-IN)
/Sensors/TC+: C32.2, P11.1 (5), R29.1, R30.2, U14.2 (Vin+), U14.6 (Vsense)
/Sensors/TC-: C32.1, P11.2 (6), R38.1, U14.4 (Vin-)
Earth: C29.2, C30.1, C31.1, P8.14, P8.16, P8.18, P8.20, P8.21, P8.22, P8.23, P8.24, P8.25, P8.26, P17.1 (+12V), R30.1, R36.1, R37.1, R38.2, U8.4 (-VS), U8.5 (REF), U12.6 (EN), U12.8, U13.6 (EN), U13.8, U14.1 (GND), U14.3 (GND), U14.5 (GND), U14.10 (GND), U14.13 (GND), U14.16 (ADDR), U14.17 (GND), U14.18 (GND), U14.21 (GND), U15.4 (-VS), U15.5 (REF); also elsewhere on the board
LC: R36.2, U15.6 (OUT); also elsewhere on the board
unnamed: R19.2, U8.8 (+RG)
unnamed: R19.1, U8.1 (-RG)
unnamed: R33.2, U15.8 (+RG)
unnamed: R33.1, U15.1 (-RG)
PT: R37.2, U8.6 (OUT); also elsewhere on the board
PT1+: P8.5, U12.13 (X0)
PT1-: P8.6, U13.13 (X0)
PT2+: P8.7, U12.14 (X1)
PT2-: P8.8, U13.14 (X1)
PT3+: P8.9, U12.15 (X2)
PT3-: P8.10, U13.15 (X2)
PT4+: P8.11, U12.12 (X3)
PT4-: P8.12, U13.12 (X3)
PT5+: P8.13; also elsewhere on the board
PT6+: P8.15; also elsewhere on the board
PT7+: P8.17; also elsewhere on the board
PT8+: P8.19; also elsewhere on the board
PT+: U8.3 (+IN), U12.3 (Y)
PT-: U8.2 (-IN), U13.3 (Y)
PT_MUX_A: U12.11 (A), U13.11 (A); also elsewhere on the board
PT_MUX_B: U12.10 (B), U13.10 (B); also elsewhere on the board
PT_MUX_C: U12.9 (C), U13.9 (C); also elsewhere on the board
SCL: R31.2, U14.19 (SCL); also elsewhere on the board
SDA: R32.2, U14.20 (SDA); also elsewhere on the board
TC_ALERT: U14.11 (Alert1); also elsewhere on the board
TC_OC: U14.9 (OCalert); also elsewhere on the board
TC_SC: U14.7 (SCalert); also elsewhere on the board
VIN: P8.3, P8.4; also elsewhere on the board

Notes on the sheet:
To Thermocouple
Pressure Transducer Connectors
PT Analog Multiplexers
To Load Cell
Thermocouple Cold Junction Compensation
Pressure Transducer Amplifier
Load Cell Amplifier

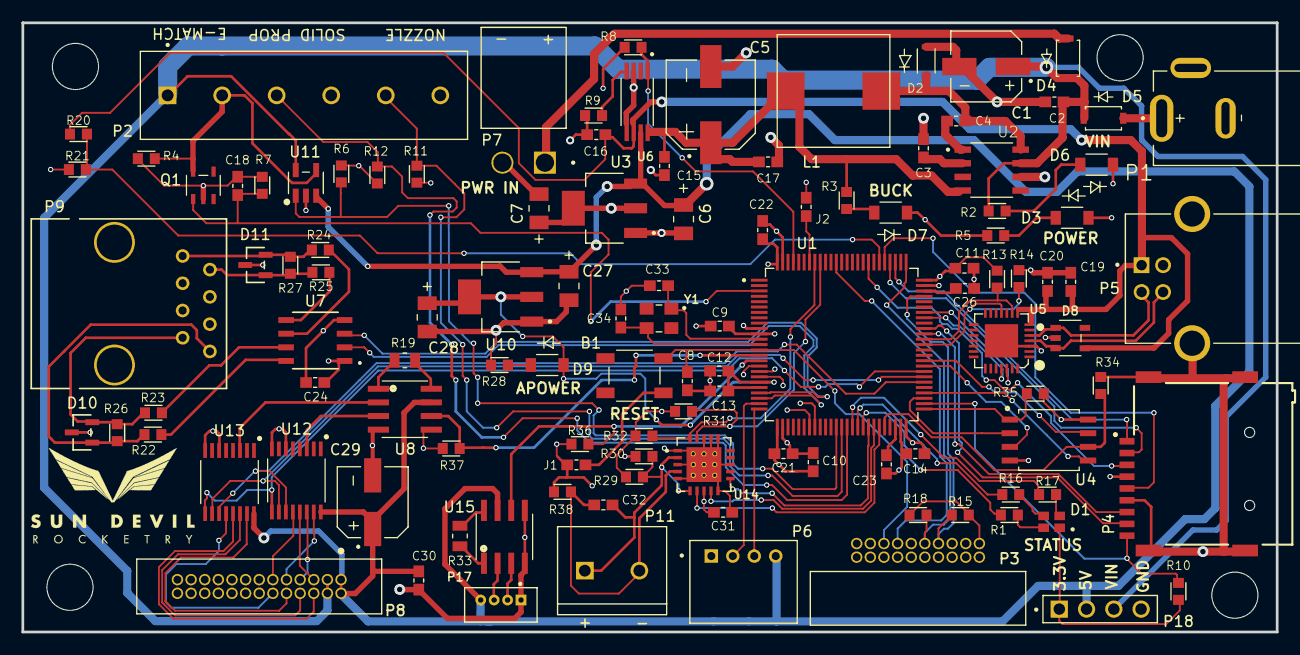
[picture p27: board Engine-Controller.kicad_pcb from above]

Board: 4 copper layers, 116.8 x 56.7 mm, 119 parts (0 on the bottom side), 103 nets.

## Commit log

2021-06-23 Added footprints and symbols for microcontroller, LED and resistor
    [Engine-Controller.kicad_pcb, Engine-Controller.sch, LQFP100-14x14mm.step]
2021-06-26 Added library files for 5V buck converter
    [NOPB.STEP]
2021-06-26 Added library files for switching capacitors
    [CAP_CL10_SAM.step, CAP_UKL_5X11_NCH.step]
2021-06-26 Added library files for switching output
    [U1-S_NCH.step]
2021-06-26 Added switching inductor to library files
    [CBC3225T220KR.STEP]
2021-06-26 Added schottky diode to libraries
    [DIO_RB160VAM_ROM.step]
2021-06-26 Added switching power supply resistors to library files
    [RC0805FR-071K54L.STEP]
2021-06-26 Added library files for 3.3 V regulator
    [NOPB.STEP]
2021-06-26 Added Tantalum Cap to library files
    [CWR11_C__KEM.step]
2021-06-26 Added USB connector to library files
    [SS-52300-001--3DModel-STEP-56544.STEP]
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2021-06-26 Added subsheet for power supply
    [Engine-Controller.sch, power.sch]
2021-06-27 Added programming connector to library files
    [1761682-3.stp, EJ508A.step, WL-SMCW-1206_rev1.stp]
2021-06-27 Added pin headers to library files
    [66953-005LF_AMP.step, LED_LTST-C150GKT_LTO.step]
2021-06-27 Added 3D file for pin header
    [901471110.stp]
2021-06-27 Added missing pins to microcontroller schematic symbol
2021-06-27 Added testpoints to library files
    [Engine-Controller.sch, Programmer.sch, USB.sch]
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2021-06-30 Completed power supply part of schematic
    [Connectors.sch, ERJ-6GEYJ474V.STEP, Engine-Controller.sch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]
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2021-06-30 Associated Schematic Symbols with footprints
    [Connectors.sch, Engine-Controller.sch, Programmer.sch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]
2021-06-30 Resolved all ERC issues
    [Connectors.sch, Engine-Controller.sch, Programmer.sch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]
2021-06-30 Added capacitor bypassing RST to ground
    [Engine-Controller.sch]
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2021-07-01 Imported footprints into layout file
    [Engine-Controller.kicad_pcb, Engine-Controller.sch, power.sch]
2021-07-03 Updated Connector pinouts and added button to Reset pin
    [Engine-Controller.sch, Programmer.sch, SW_PTS647SM38SMTR2LFS_CNK.step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]
2021-07-03 Added buffer to some IOs
    [Connectors.sch, Engine-Controller.sch, Programmer.sch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]
2021-07-03 Added NO Jumper to NRST button
    [Connectors.sch, Engine-Controller.sch]
2021-07-03 Fixed J1 orientation
    [Engine-Controller.sch]
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2021-07-04 Added Micro SD Card
    [Engine-Controller.sch, Flash_SD.sch, MEM2075-00-140-01-A.stp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]
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2021-07-04 Moved Programmer to connectors sheet
    [Connectors.sch, Engine-Controller.sch, Flash_SD.sch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]
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2021-07-04 Added Digital Signals for Flash
    [Engine-Controller.sch]
2021-07-04 Fixed Schematic ERC erros
    [Connectors.sch, Engine-Controller.sch, Flash_SD.sch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]
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2021-07-06 Resolved DRC issues
    [Connectors.sch, Engine-Controller.kicad_pcb]
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2021-07-06 Added in Micro 3D model to step file
    [Engine-Controller.kicad_pcb, NOPB.STEP, SOT-223.STEP]
2021-07-10 Added source selector schottky to lib files
    [SOD-123FL_MCC.step]
2021-07-10 Added voltage source selector to schematic
    [Connectors.sch, power.sch]
2021-07-10 Updated buck converter schottky symbol
    [power.sch]
2021-07-10 Grounded 12V barrel plug detect pin to GND
    [power.sch]
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2021-07-13 Added power multiplexor to lib files
    [TPS2115APWR.step]
2021-07-13 Wired 5V power multiplexor
    [Engine-Controller.sch, USB.sch, power.sch]
2021-07-13 Annotated 5V selector parts
    [power.sch]
2021-07-13 Connected symbols to footprints
    [power.sch]
2021-07-13 Added new components to PCB
    [Engine-Controller.kicad_pcb]
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2021-07-20 Added new C1 cap to PCB layout
    [Engine-Controller.kicad_pcb, power.sch]
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2021-07-24 Removed SWD 3.3V connections
    [Connectors.sch, Engine-Controller.kicad_pcb, SRP1038A-330M.FCStd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]
2021-07-24 Finished Routing Rev 2 changes
    [Engine-Controller.kicad_pcb]
2021-07-24 Added silkscreen header labels and SDR Logo
    [Engine-Controller.kicad_pcb, SRP1038A-330M.stp]
2021-07-24 Fixed issue with PCB images
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2021-09-22 Changed MCU from M4 to M7
    [Connectors.sch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]
2021-09-22 Added polarity marking to C1
    [SML-LX1206GC-TR.step, power.sch]
2021-09-22 Removed resistor divider from buck converter
    [EEEFP1E151AL.STEP, power.sch]
2021-09-22 Added LEDs to all power rails
    [power.sch]
2021-09-22 changed labels in schematic
    [Connectors.sch, Engine-Controller.sch, power.sch]
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2021-11-07 Add Internal regulator stability caps
    [Engine-Controller.sch, Ignition.sch]
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2021-11-10 Added logo and mounting hole to lib and schematic
    [Connectors.sch]
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2022-01-03 fixed colors on connectors
    [282837-6.STEP, 901471110.stp, Engine-Controller.kicad_pcb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]
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2022-02-06 added rgb led, and deleted old status led
    [Connectors.kicad_sch, Engine-Controller.kicad_sch]
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2022-03-07 merged all non power components into single sheet
    [Engine-Controller.kicad_sch, Page2.kicad_sch]
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2022-03-07 Added connectors for valve controller and main power line
    [Engine-Controller.kicad_sch, Page2.kicad_sch, power.kicad_sch]
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2022-03-11 added multiplexor and analog switch to lib files
    [MAX4617EUE.step, MC74HC4066ADG.step]
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2022-04-27 corrected comparator symbol pin numbers
    [Engine-Controller.kicad_sch, Page2.kicad_sch, Sensors.kicad_sch]
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2022-04-27 fixed pinout of MOSFET symbol
    [Engine-Controller.kicad_sch, Page2.kicad_sch, Sensors.kicad_sch]
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2022-05-11 added pull up resistor to flash SS pin
    [Engine-Controller.kicad_sch, Page2.kicad_sch, Sensors.kicad_sch]
2022-05-12 added crystal oscillator to lib files
    [ECS-240-12-37B-CKY-TR.step, Engine-Controller.kicad_sch, Sensors.kicad_sch]
2022-05-12 changed crystal oscillator
    [ECS-240-12-37B-CKY-TR.step, ECS-240-18-33-JGN-TR.STEP]
2022-05-12 added crystal oscillator to schematic
    [Engine-Controller.kicad_sch]
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2022-05-13 fixed border of usb scheamtic section
    [Page2.kicad_sch, Sensors.kicad_sch]
2022-05-13 resolved all ERC schematic issues
    [Engine-Controller.kicad_sch, Page2.kicad_sch, Sensors.kicad_sch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]
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2022-05-13 added safety switch screw terminal to lib files
    [282837-2.step]
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2022-05-15 resolved minor DRC errors
    [Engine-Controller.kicad_pcb]
2022-05-16 changed TC connector to be different from power connector
    [532580229.stp, Engine-Controller.kicad_pcb, Engine-Controller.kicad_sch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]
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2022-05-22 moved uart chip decoupling capacitors closer to IC pins
    [Engine-Controller.kicad_pcb]
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2023-06-09 added legacy parts from Rev 2.0 to lib files
    [SBH11-PBPC-D05-RA-BK.STEP]

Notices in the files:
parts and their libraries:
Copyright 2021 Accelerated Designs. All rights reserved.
